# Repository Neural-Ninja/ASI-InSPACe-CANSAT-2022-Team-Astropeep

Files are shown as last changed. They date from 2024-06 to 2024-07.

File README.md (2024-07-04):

# ASI-InSPACe-CANSAT-2022-Team-Astropeep

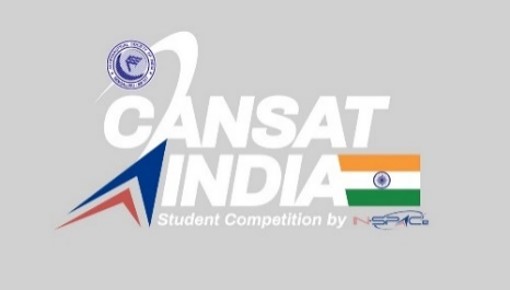
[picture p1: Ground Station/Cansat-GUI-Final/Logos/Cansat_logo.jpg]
CANSAT Design


This repository contains the project documentation and code for our team's (Team Astropeep) CanSat developed for the CanSat-India 2022 competition organized by Astronautical Society of India [(ASI)](https://www.asindia.org/), Indian National Space Promotion and Authorization Centre [(IN–SPACe)](https://www.inspace.gov.in) and Indian Space Research Organization [(ISRO)](https://www.isro.gov.in/). A CanSat is a miniature version of a real satellite, designed to fit within a small volume. Despite its miniature size, it mimics many of the functionalities and challenges of actual satellites. It is designed to perform specific scientific and engineering tasks, typically in a controlled flight environment such as a rocket launch or high-altitude balloon release. CanSats are used primarily in educational settings, particularly in STEM (Science, Technology, Engineering, and Mathematics) education programs, to teach students about satellite technology, space missions, data collection, and analysis.

## Introduction

This project details the development of our CanSat for the CanSat-India competition. Our goal was to design and build a functioning satellite within the constraints provided by the competition guidelines.

## Features

- Compact size (fits within a standard soda can)
- Integration of various sensors (e.g., temperature, pressure)
- Communication systems for data transmission
- Parachute deployment system
- Mechanical Gyro Control
- Data logging capabilities

## Components

The CanSat consists of the following main components:

- **Microcontroller**: Controls the operation and data collection.
- **Sensors**: Measure various environmental parameters (e.g., temperature, pressure).
- **Communication System**: Transmits data to the ground station.
- **Power System**: Provides necessary power to all components.
- **Mechanical Structure**: Holds all components securely and includes the parachute deployment system.
- **Mechanical Gyro Control**: Controls the orientation of CanSat during Descent.

## Technical Details

- **Microcontroller**: We used ESP-32 for processing and data handling.
- **Sensors**: Included BMP-280, DHT11 and MPU6050 to gather environmental data during flight.
- **Communication**: XBEE-Pro-S2C was employed for transmitting data to the ground station with 2.4 GHz of operating frequency.
- **Power**: Two Li-Ion battery (9V and 1200 mAh) was used to power the CanSat throughout its mission.

## Flight Software

The `Flight Software Files/` directory contains the source code used in the CanSat. It includes:

- **Main Control Code**: Handles sensor readings, data transmission, and overall control.
- **Sensor Calibration Scripts**: Scripts used for calibrating sensors pre-flight.
- **Data Logging Code**: Code snippets responsible for logging data during the flight.

## Ground Station

The `Ground Station/` directory contains the source code used in developing the ground station and GUI of CanSat. It includes:

- **GUI Scripts**: Handles sensor readings, data transmission, and overall control.
- **Communication Scripts**: Scripts used for calibrating sensors pre-flight.
- **Data Logging Code**: Code snippets responsible for logging data during the flight.

## 

## Usage

To replicate our CanSat project or use parts of our code, follow these steps:

1. Clone this repository:
    ```bash
       git clone https://github.com/Neural-Ninja/ASI-InSPACe-CANSAT-2022-Team-Astropeep.git
       cd ASI-InSPACe-CANSAT-2022-Team-Astropeep
2. Navigate to the `CANSAT Design Files/` directory for acessing the design CAD files.
     ```bash
        cd CANSAT Design Files
3. Navigate to the `CANSAT Presentation Files/` and `CANSAT Report Files/` for better conceptual understanding of our CANSAT model and its working. 
     ```bash
        cd CANSAT Presentation Files
        cd CANSAT Report Files
4. Navigate to the `Flight Software Files/` for accessing the Flight Software source codes.
    ```bash
        cd Flight Software Files
5. Navigate to the `Ground Station/` for accessing the Ground Station source codes
    ```bash
        cd Ground Station
## Contributing

Contributions to improve the code, documentation, or any other aspect of the project are welcome. Feel free to fork this repository, make your changes, and submit a pull request.

## License

This project is licensed under the [MIT License](License) - see the LICENSE file for details.

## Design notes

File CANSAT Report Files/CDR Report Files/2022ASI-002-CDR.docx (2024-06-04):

CANSAT 2022-23

Critical Design Review

(CDR)

TEAM ID: 2022ASI-002

TEAM NAME: ASTROPEEP

Serial N0. | CONTENTS
| Team description
| Sponsorship to CANSAT
| List of Acronyms
| System Overview
| Sensor Summary
| Mechanical Material Selection & Overview
| Mechanical Subsystem Analysis & Results
| Power Budget
| Mass Budget
| Actuator Design
| Control Mechanism of Gyroscope
| Trajectory & Descent Control
| Sensor Testing
| Communication & Data Handling
| Electrical Power Subsystem
| Flight Software Design
| GCS Deign & Over View
| CANSAT Algorithm
| Ground Station Final test Results
| CANSAT Ready to launch & Final test result
| CANSAT Integration & Testing
| Mission Operation and analysis
| Pre-flight requirement-check analysis
| Logistics and Transportation
| CANSAT ready to launch and final comments
| Conclusion

Team Description

FACULTY ADVISOR
Dr. Abhishek Rawat
MENTOR
Dr. Jagat Joyti Rath
MENTOR
Dhaval Joshi

Communication and Data handling
Risabh Raushan
Purvang Mistry
Akash Payghan
Ashotosh Jha
Software
Ashutosh Jha
Electronics
Akash Payghan
Victor Azad
Somesh Swami
Mechanical Analysis
Anuj Kumar Jha
Anuj Jha
TEAM LEADER
Victor Azad
Mechanical Design
Sagar Parihar
Victor Azad
Somesh Swami
Victor Azad
Ashutosh Jha

Sponsorship to CANSAT

We as Team Astropeep have received the sponsorship from different organisation and institutions, in form of money and in the form of goods.

List of sponsors are as mentioned below:

1. Institute of Infrastructure Technology Research and Management, Ahmedabad
2. Centre of Advanced Defence Technologies, IITRAM, Ahmedabad
3. Indian Studytech Services Pvt. Ltd., Dholpur, Rajasthan
4. Rudrabots Pvt. Ltd., Ahmedabad

List of Acronyms

Acronyms | Meaning
3D | 3-Dimensional
A | Analysis
cm | Centimeter
D | Demonstration
dB | Decibel
EPS | Electrical power Subsystem
FRR | Flight Readiness Review
FSW | Flight Software
GCS | Ground Control System
gm | Gram
GPS | Global Positioning System
GS | Ground Station
GUI | Graphical User Interface
Hz | Hertz
I | Inspection
I2C | Inter-Integrated Circuit
IC | Integrated Circuits
LED | Light Emitting Diode
PC | Personal Computer
QHA | Quasi Harmonic Function
RTC | Real Time Clock
T | Test
VM | Verification Method
GHz | Giga Hertz
s | Second
csv | Comma separated values
hrs | Hours
PCB | Printed Circuit Board
mAh | Milli ampere hour
m | Meter
V | Volts
FSS | Flight Software State

System Overview

MISSION SUMMARY

- Innovative Mechanical Gyro-control system that shall demonstrate the descent control of the CANSAT.
- CANSAT descent control system that shall open at an altitude of 500 m.

CANSATs will be launched to an altitude of 800.0 m to 900.0 m from the ground level and above the launch site & deployed near the peak altitude. During the ejection from the rocket orientation of the CANSAT is not controlled. The CANSAT must remain intact during the course of the entire mission and send the data to the ground station through a telemetry link.

Sr.no. | Requirement | Priority | Fulfillment | VM
| | | | A | I | T | D
1 | Total mass of the CANSAT shall be under 0.700 kg (+/- 0.050 kg) | High | Mass of Cansat is within limits. | x | | | X
2 | CANSAT shall fit in a cylindrical body of 0.125 m diameter x 0.310 m height. Tolerances are to be included to facilitate container deployment from the rocket fairing. | High | Cansat is designed with appropriate dimensions. | X | | | X
3 | Any sharp edges on the container body shall be avoided as it can cause interfere during the CANSAT ejection from the rocket. | High | No sharp Edges are present. | X | | | X
4 | Color of the CANSAT body shall be fluorescent i.e., pink, red or orange, and shall embody the Indian flag. | High | Color will be fluorescent and will embody Indian Flag. | | | | X
5 | The CANSAT shall consist of necessary sensors to provide the following mandatory Real-time datasets: Position data, altitude, pressure, temperature, orientation data, power data & system status. | High | Cansat has necessary sensors required for measuring mandatory data. | X | | | X
6 | Each data field shall be displayed in real-time on the ground station user interface/software. | High | GUI will be developed for displaying Data.
7 | CANSAT shall also record the data and save it into an onboard SD card in case of telemetry connection loss. | High | The data shall be recorded in SD Card.
8 | All electronics shall be enclosed and shielded from the environment. No electronics can be exposed except for sensors. There must be a structural enclosure. | High | No Electronics is exposed. | x | | | X
9 | CANSAT structure shall be built to survive 15 Gs of launch acceleration & 30 Gs of shock. | High | CANSAT will survive required shock. | | | | X
10 | The CANSAT shall have an external power switch with an indicator light or sound for being turned on or off, in order to avoid the de-assembling of CANSATs on the launch pad. | High | CANSAT has an external power switch. | x | | | X
11 | The CANSAT shall contain a total of 2 descent control mechanisms, to be used at different stages while descent. | High | has 2-descent control mechanism. | | | | x
12 | CANSAT shall immediately deploy the first parachute after ejection from the rocket. | High | 1st parachute will be immediately deployed after ejection. | | | | X

# Sensor Systems Summary and Test results

Selected Component | Type | Function | Interface
Adafruit BMP 280 | Pressure and temperature sensor | Measures air pressure and temperature both in the payload and the container | I2C
Matek SAM M8Q | GPS | Gets payload coordinates (latitude and longitude), GPS time, and GPS satellite | Serial
Voltage divider | Voltage Sensor | Measures voltage of the payload’s battery | ADC
MPU6050 | Acceleration and Orientation Sensor | Orientation and Acceleration Measurement | ADC

Sensor | Model | Function
Altimeter Sensor | BMP280 | Altitude Measurement
Air Pressure and Air Temperature Sensor | BMP280 | Pressure and Temperature Measurement
Acceleration and Orientation Sensor | MPU6050 | Orientation and Acceleration Measurement
GPS Receiver Sensor | Matek SAM M8Q | Latitude, Longitude, Altitude, Time, Satellites number Measurement
Voltage Sensor | Voltage Divider , CPU’s ADC Converter | Power Status

# Payload Air Pressure Sensor

# Summary (1 of 2)

Sensor-Adafruit BMP 280

Pressure Range (hPa) | Operating Voltage (V) | Weight (g) / Dimension (mm) | Current Consumption (uA) | Resolution (Pa) | Accuracy (hPa) | Interface | Data Format
300-1250 | 1.65 – 3.6 | 1.2 21.6 x 16.6 | 2.7 | 0.016 | ±0.08 | I2C, SPI | Float XXXXX.XX (Pa)

Altitude above sea level can be calculated from Barometric Equation below. However, output from sensor is very noisy so that a kalman filter will be used to estimate the pressure value.

Barometric Equation

# Descent Control Design

Sample Output

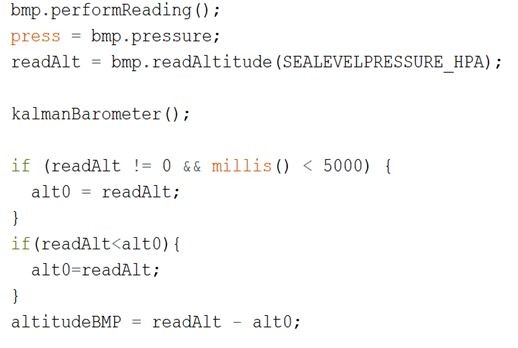
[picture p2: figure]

Kalman Filter

Data Processing

Sensor | | | | Adafruit BMP 280
Temperature Range (°C) | Operating Voltage (V) | Weight (g) / Dimension (mm) | Current Consumption (uA) | | Resolution (Pa) | Accuracy (hPa) | Interface | Data Format
0 – 65 | 1.65 – 3.6 | 1.2 21.6 x 16.6 | 2,7 | | 0.016 | ±0.08 | I2C, SPI | Float XX.XX (C)

# Payload Air Pressure Sensor Summary

# (2 of 2)

# Temperature data will be collected and processed with the help of Adafruit_BMP3XX library. No further processing is needed as the reading is very stable.

Sample Output

Data Processing

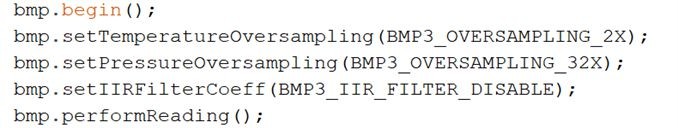
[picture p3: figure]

# GPS Sensor Summary

Sensor | Matek SAM M8Q + Compass

Tracking Sensitivity (dBm) | Operating Voltage (V) | Weight (g) / Size (mm) | Current Consumption (mA) | Channel | Accuracy (m) | Interface | Update Rate (Hz) | Data Format
-165 | 4-6 | 7 20 x 20 x 10 | 29 | 72 | ~2.5 | UART | 18 | Float and Integer

Longitude, latitude, and the other data will be collected and processed with the help of Tiny GPS Plus library by Mikal Hart. This sensor can lock onto GPS satellite quickly.

Data Processing

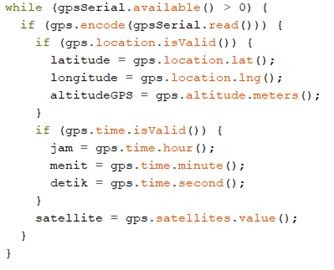
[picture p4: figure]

Sample Output

# Left to right:

# Hour, minute, second, latitude, longitude, altitude, satellite

Source: https://github.com/mikalhart/TinyGPSPlus/blob/master/src/TinyGPS%2B%2B.h

# Payload Voltage Sensor Summary

Name | Range (V) | Error rate (%) | Interface | Data Format
Processor Analog Pin (Voltage Divider) | 0 - 5 | 0.03 | ADC | Float X.XX (Volt)

# Battery voltage is measured using the ADC port trough a voltage divider, the following resistors are used in the circuit.

R1 = 1 MΩ

R2 = 100 kΩ

The ATSAMD Processor ADC has maximum resolution of 32-bit with 3.3 volt analog reference, but the resolution used is 16-bit resolution. So, the maximum accuracy of this on board voltage sensor is 50 uV..

Sample Output

Data Processing

# Gyroscope Sensor Selection Summary :

Sensor | Range (°/s) | Resolution (bit) | Accuracy (°/s) | Data Interface | Operating Voltage (V) | Cost (Rs.) | Dimension (mm) | Weight (gm)
MPU6050 | ±250 | 16 | 1.9 | I2C/IIC | 3-5 | 120 | 4 X 4 X 0.9 | 3

# Reason for selecting MPU6050 :

# Light weight, small size and Low Cost.

# Using same sensor for acceleration and orientation measurement will reduce the cost and weight of Cansat.

Team Id:2022ASI-002 AstroPeep

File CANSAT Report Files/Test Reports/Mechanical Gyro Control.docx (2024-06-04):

# Control Mechanism of Gyroscope

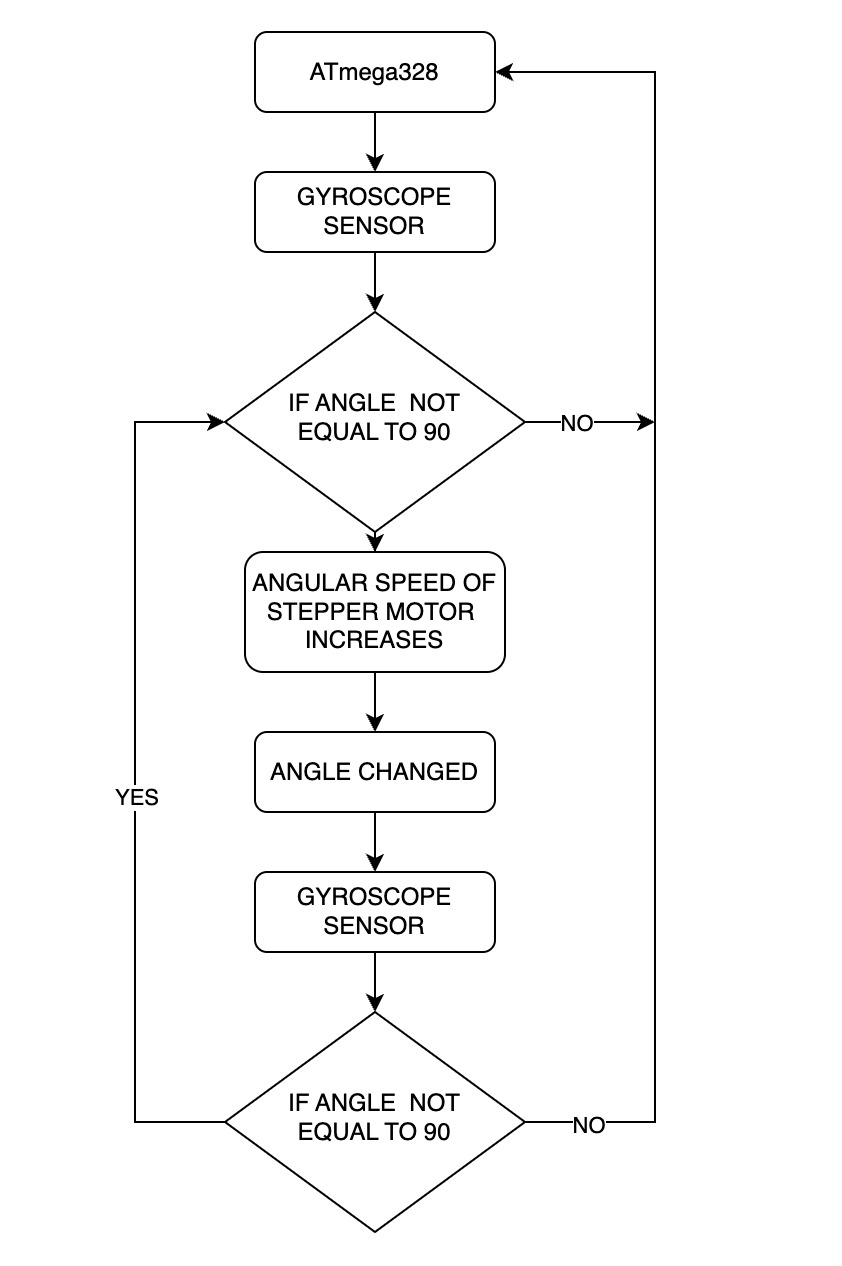
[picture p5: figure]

With the help of ATMEGA-328, gyroscope sensor detect the orientation of our CANSAT. If the angle detected by gyroscopic sensor is not equal to 90 ° i.e., our CANSAT is not perfectly straight then the angular speed of stepper motor attached to our gyroscope increases and thus our gyroscope applied force on the CANSAT to make it perpendicular. The angular speed increases uptill the CANSAT is not aligned perpendicularly.

Once our CANSAT is aligned perpendicularly the angular speed of stepper motor remains constant. Whenever an external force is applied to our CANSAT, accordingly the speed of stepper motor increases or decreases in order to align our CANSAT 90 ° .

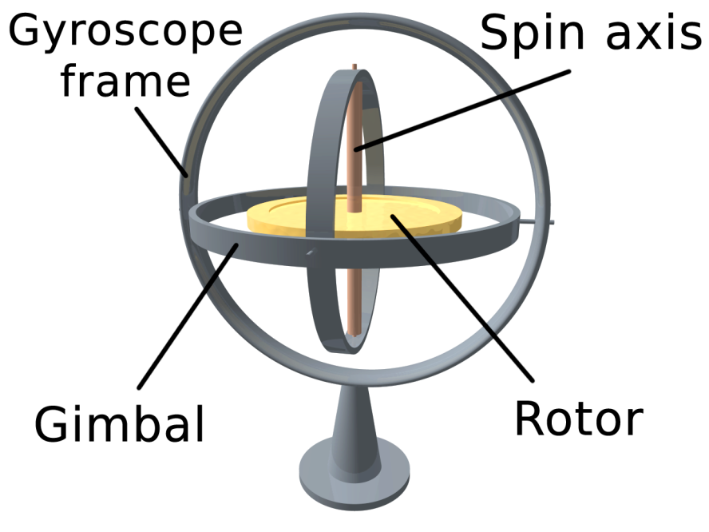
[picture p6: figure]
Gyroscope - Wikipedia

CANSAT India Students Competition by ASI: Team Id:2022ASI-002 AstroPeep

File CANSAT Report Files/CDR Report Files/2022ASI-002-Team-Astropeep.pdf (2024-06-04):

# CANSAT 2022-23

Team Id:2022ASI-002
AstroPeep

# Critical Design Review (CDR)

# TEAM ID: 2022ASI-002

# TEAM NAME: ASTROPEEP

Team Id:2022ASI-002

AstroPeep

## Serial N0. CONTENTS

## 1. Team description

## 2. Sponsorship to CANSAT

## 3. List of Acronyms 4. System Overview

## 5. Sensor Summary 6. Mechanical Material

| Selection & Overview

## 7. Mechanical Subsystem

| Analysis & Results

## 8. Power Budget 9. Mass Budget

## 10. Actuator Design

## 11. Control Mechanism of

| Gyroscope

## 12. Trajectory & Descent Control

## 13. Sensor Testing

## 14. Communication & Data

| Handling

## 15. Electrical Power Subsystem

## 16. Flight Software Design

## 17. GCS Deign & Over View

## 18. CANSAT Algorithm

Team Id:2022ASI-002

AstroPeep

## 19. Ground Station Final test Results 20. CANSAT Ready to launch & Final test result

## 21. CANSAT Integration & Testing

## 22. Mission Operation and analysis

## 23. Pre-flight requirement-check analysis 24. Logistics and Transportation 25. CANSAT ready to launch and final comments 26. Conclusion

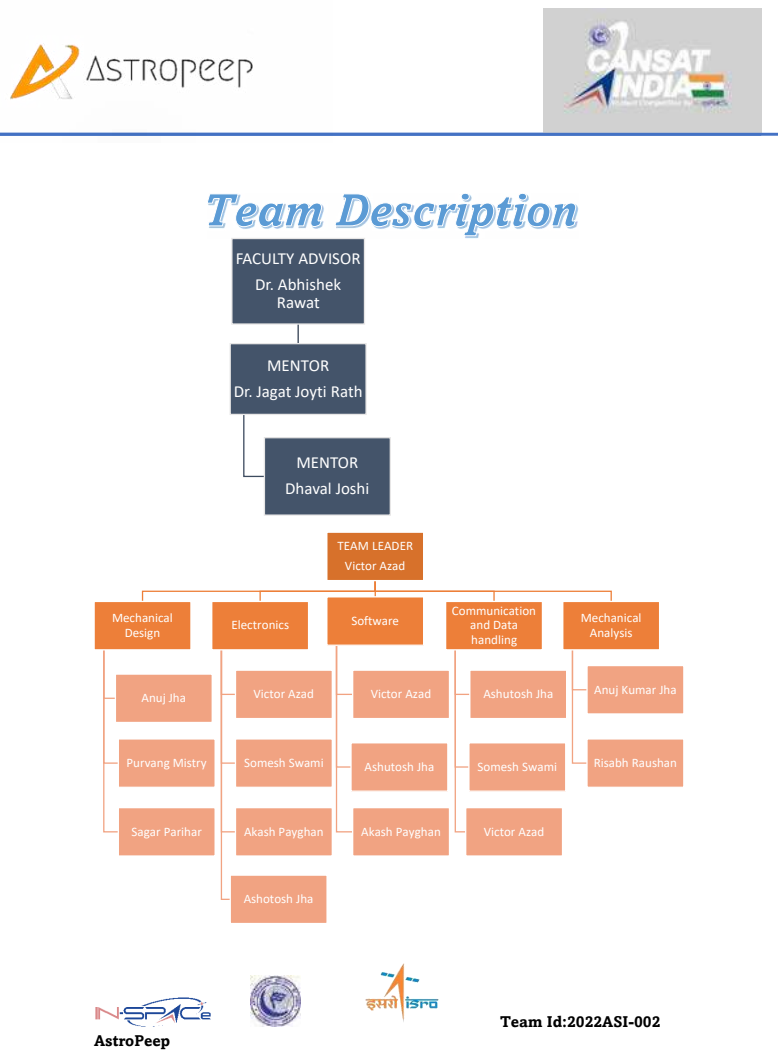
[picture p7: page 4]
Team Id:2022ASI-002; AstroPeep; FACULTY ADVISOR; Dr. Abhishek Rawat; MENTOR; Dhaval Joshi; TEAM LEADER; Victor Azad; Mechanical Design; Anuj Jha; Purvang Mistry; Sagar Parihar; Electronics; Somesh Swami; Akash Payghan; Ashotosh Jha; Software; Ashutosh Jha; Communication and Data handling; Mechanical Analysis; Risabh Raushan

MENTOR
Dr. Jagat Joyti Rath

Anuj Kumar Jha

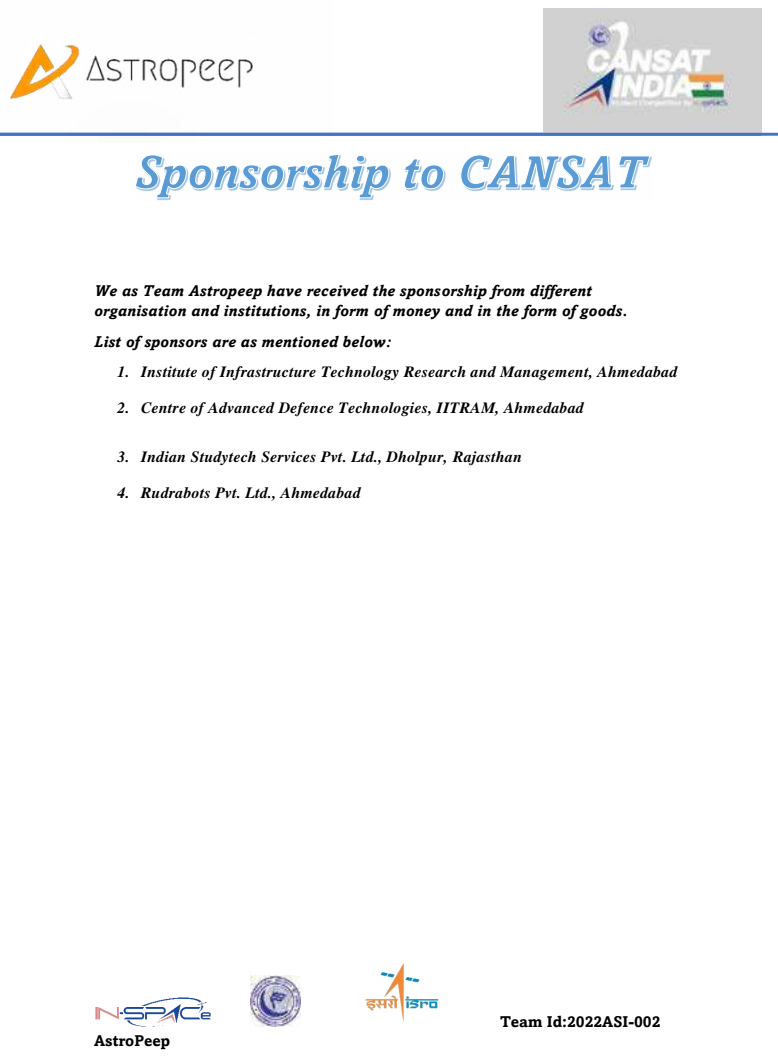
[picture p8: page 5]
Team Id:2022ASI-002; AstroPeep

We as Team Astropeep have received the sponsorship from different
organisation and institutions, in form of money and in the form of goods.

List of sponsors are as mentioned below:

1. Institute of Infrastructure Technology Research and Management, Ahmedabad

2. Centre of Advanced Defence Technologies, IITRAM, Ahmedabad

3. Indian Studytech Services Pvt. Ltd., Dholpur, Rajasthan

4. Rudrabots Pvt. Ltd., Ahmedabad

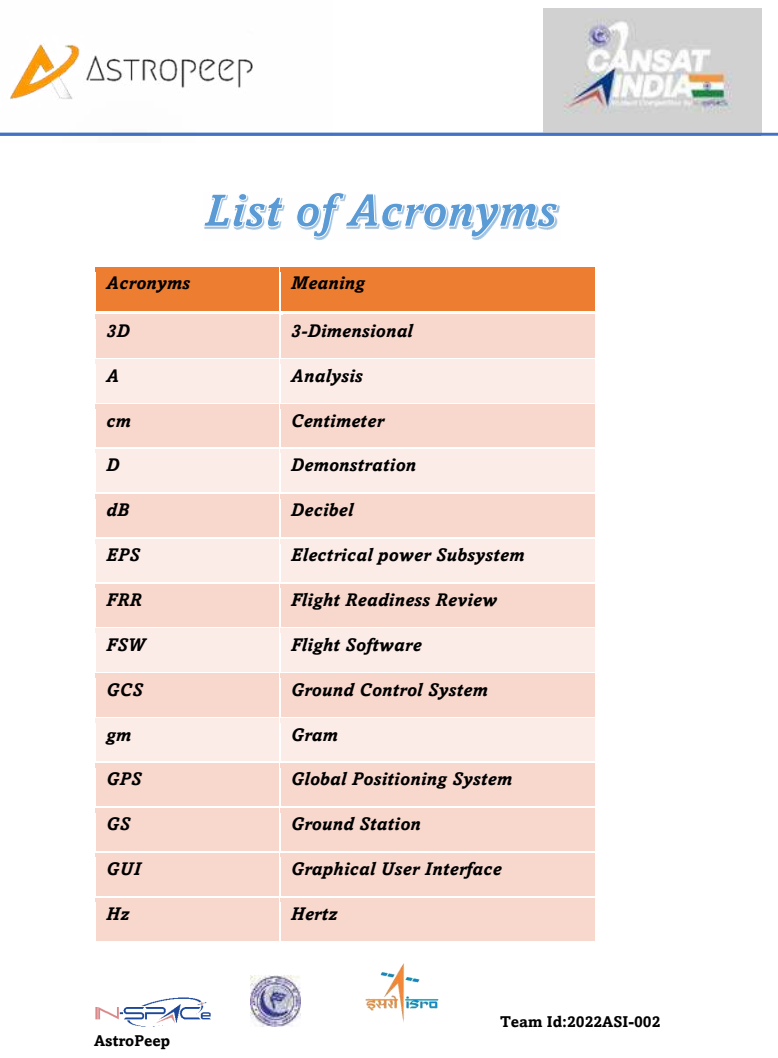
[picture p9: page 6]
Team Id:2022ASI-002; AstroPeep; Acronyms; Meaning; 3-Dimensional

A Analysis

cm | Centimeter

D Demonstration

dB | Decibel

EPS | Electrical power Subsystem

FRR | Flight Readiness Review

FSW | Flight Software

GCS | Ground Control System

gm | Gram

GPS | Global Positioning System

GS | Ground Station

GUI | Graphical User Interface

Hz | Hertz

Team Id:2022ASI-002

AstroPeep

I Inspection

I2C | Inter-Integrated Circuit
IC | Integrated Circuits
LED | Light Emitting Diode
PC | Personal Computer
QHA | Quasi Harmonic Function
RTC | Real Time Clock

T Test

VM | Verification Method
GHz | Giga Hertz
s | Second
csv | Comma separated values
hrs | Hours
PCB | Printed Circuit Board
mAh | Milli ampere hour
m | Meter

V Volts

FSS | Flight Software State

Team Id:2022ASI

-002

AstroPeep

Team Id:2022ASI-002

AstroPeep

MISSION SUMMARY

- Innovative Mechanical Gyro-control system that shall demonstrate the

descent control of the CANSAT.

- CANSAT descent control system that shall open at an altitude of 500

m.

CANSATs will be launched to an altitude of 800.0 m to 900.0 m from the ground

level and above the launch site & deployed near the peak altitude. During the

ejection from the rocket orientation of the CANSAT is not controlled. The

CANSAT must remain intact during the course of the entire mission and send the

data to the ground station through a telemetry link.

Sr.no. | Requirement | Priorit y | Fulfillment | VM
A | I | T | D
1 Total mass of the CANSAT shall be | under 0.700 kg (+/- 0.050 kg) | High | Mass of Cansat is within limits. | x | X
2 CANSAT shall fit in a cylindrical | body of 0.125 m diameter x 0.310 m height. Tolerances are to be included to facilitate container deployment from the rocket fairing. | High | Cansat is designed with appropriate dimensions. | X X
3 Any sharp edges on the container | body shall be avoided as it can cause interfere during the CANSAT ejection from the rocket. | High | No sharp Edges are present. | X X

Team Id:2022ASI-002

AstroPeep

4 Color of the CANSAT body shall be | fluorescent i.e., pink, red or orange, and shall embody the Indian flag. | High | Color will be fluorescent and will embody Indian Flag. | | X
5 The CANSAT shall consist of | necessary sensors to provide the following mandatory Real-time datasets: Position data, altitude, pressure, temperature, orientation data, power data & system status. | High | Cansat has necessary sensors required for measuring mandatory data. | X X
6 Each data field shall be displayed | in real-time on the ground station user interface/software. | High | GUI will be developed for displaying Data.
7 CANSAT shall also record the data | and save it into an onboard SD card in case of telemetry connection loss. | High | The data shall be recorded in SD Card.
8 All electronics shall be enclosed and | shielded from the environment. No electronics can be exposed except for sensors. There must be a structural enclosure. | High | No Electronics is exposed. | x | X
9 CANSAT structure shall be built to | survive 15 Gs of launch acceleration & 30 Gs of shock. | High | CANSAT will survive required shock. | | X
10 The CANSAT shall have an external | power switch with an indicator light or sound for being turned on or off, in order to avoid the de-assembling of CANSATs on the launch pad. | High | CANSAT has an external power switch. | x | X
11 The CANSAT shall contain a total | of 2 descent control mechanisms, to be used at different stages while descent. | High | has 2-descent control mechanism. | | x

Team Id:2022ASI-002

AstroPeep

### 12 CANSAT shall immediately deploy

the first parachute after ejection from the rocket.

High 1st parachute will be immediately deployed after ejection.

X

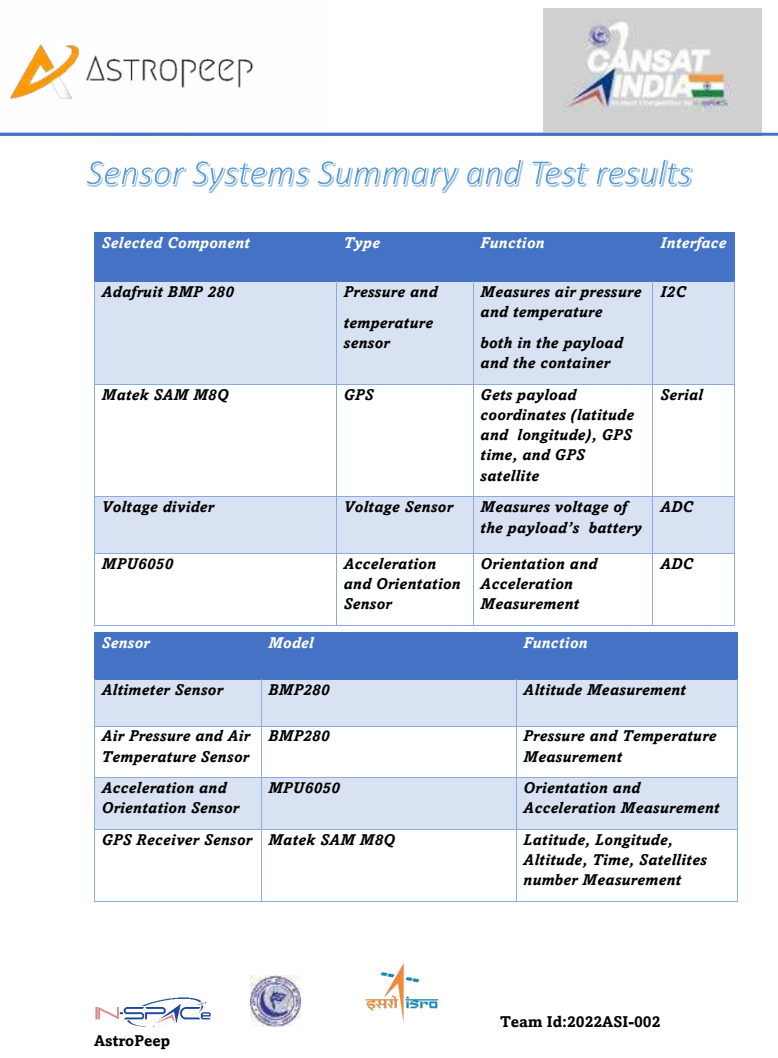
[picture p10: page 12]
Team Id:2022ASI-002; AstroPeep; Selected Component; Type; Function; Interface; Sensor; Model

Adafruit BMP 280 | Pressure and temperature sensor | Measures air pressure and temperature both in the payload and the container | I2C

Matek SAM M8Q | GPS | Gets payload coordinates (latitude and longitude), GPS time, and GPS satellite | Serial

Voltage divider | Voltage Sensor | Measures voltage of the payload’s battery | ADC

MPU6050 | Acceleration and Orientation Sensor | Orientation and Acceleration Measurement | ADC

Altimeter Sensor | BMP280 | Altitude Measurement

Air Pressure and Air Temperature Sensor | BMP280 | Pressure and Temperature Measurement

Acceleration and Orientation Sensor | MPU6050 | Orientation and Acceleration Measurement

GPS Receiver Sensor | Matek SAM M8Q | Latitude, Longitude, Altitude, Time, Satellites number Measurement

Team Id:2022ASI-002

AstroPeep

Voltage Sensor | Voltage Divider , CPU’s ADC Converter

Power Status

Team Id:2022ASI-002

AstroPeep

# Payload Air Pressure Sensor Summary (1 of 2)

## Sensor-Adafruit BMP 280

Pressure
Range
(hPa)

Operating
Voltage
(V)

Weight (g)
/
Dimension
(mm)

Current
Consumption
(uA)

Resolution
(Pa)

Accuracy
(hPa)

Interface Data
Format

300-
1250

1.65 – 3.6 1.2

### 21.6 x

16.6

2.7 | 0.016 | ±0.08 | I2C, SPI | Float XXXXX.XX (Pa)

Altitude above sea level can be calculated from Barometric Equation below. However, output from sensor is very noisy so that a kalman filter will be used to estimate the pressure value.

## Barometric Equation

## Sample Output

### Data Processing

Team Id:2022ASI-002
AstroPeep

### Kalman Filter

Team Id:2022ASI-002

AstroPeep

# Payload Air Pressure Sensor Summary

(2 of 2)

## Temperature data will be collected and processed with the help of

## Adafruit_BMP3XX library. No further processing is needed as the

reading is very stable.

# GPS Sensor Summary

Sensor | Adafruit BMP 280
Temperature Range (°C) | Operating Voltage (V) | Weight (g) / Dimension (mm) | Current Consumption (uA) | Resolution (Pa) | Accuracy (hPa) | Interface | Data Format
0 – 65 | 1.65 – 3.6 | 1.2 21.6 x 16.6 | 2,7 | 0.016 | ±0.08 | I2C, SPI | Float XX.XX (C)
Data Processing | Sample Output

Tracking Sensitivity (dBm); Operating Voltage (V); Weight (g) / Size (mm); Current Consumption (mA); Channel Accuracy (m); Interface Update Rate (Hz); Data Format; UART; Float; and Integer

Team Id:2022ASI-002

AstroPeep

Sensor | Matek SAM M8Q + Compass

Longitude, latitude, and the other data will be collected and processed with the help of Tiny GPS Plus library by Mikal Hart. This sensor can lock onto GPS satellite quickly.

## Data Processing

Team Id:2022ASI-002

AstroPeep

# Left to right:

Hour, minute, second, latitude, longitude,

# altitude, satellite

# Payload Voltage Sensor Summary

Name | Range (V) | Error rate (%) | Interface | Data Format
Processor Analog Pin (Voltage Divider) | 0 - 5 | 0.03 | ADC | Float
| | | | X.XX (Volt)

## Battery voltage is measured using the ADC port trough a voltage

divider, the following resistors are used in the circuit.

## R1 = 1 MΩ

## Sample Output

### Source: https://github.com/mikalhart/TinyGP SPlus/blob/master/src/TinyGPS%2B %2B.h (https://github.com/mikalhart/TinyGPSPlus/blob/master/src/TinyGPS%2B%2B.h)

Team Id:2022ASI-002

AstroPeep

## R2 = 100 kΩ

The ATSAMD Processor ADC has maximum resolution of 32-bit with 3.3 volt analog reference, but the resolution used is 16-bit resolution. So, the maximum accuracy of this on board voltage sensor is 50 uV..

## Data Processing

## Sample Output

Team Id:2022ASI-002

AstroPeep

# Gyroscope Sensor Selection Summary :

Sensor | Range (°/s) | Resolution (bit) | Accuracy (°/s) | Data Interface | Operating Voltage (V) | Cost (Rs.) | Dimension (mm) | Weight (gm)
MPU6050 | ±250 | 16 | 1.9 | I2C/IIC | 3-5 | 120 | 4 X 4 X 0.9 | 3

## Reason for selecting MPU6050 :

➢Light weight,small size and Low Cost.

## ➢Using same sensor for acceleration and orientation measurement will reduce the cost and weight of

Cansat.

CANSAT India Students Competition by ASI:

Team Id:2022ASI-002 AstroPeep

# Innovative Materials Selection:

## Material Proposed as in PDR:

As in Preliminary Design Report (PDR) of our CANSAT had:

Serial No. | Component | Previous Material | Modified material
1. | Outer Body Panels | ABS Polycarbonate Sheets | ABS Polycarbonate Sheets
2. | Vertical Rods | 2024 T3 Al Alloy | CFRP Z-100
3. | Horizontal Bases | 2024 T3 Al Alloy | CFRP Z-100
4. | Circular Support Rings | -- | CFRP Z-100
5. | Top Lid | Polyethene Film | Polyethene Film
6. | Parachute & Chords | Ripstop Nylon | Ripstop Nylon

Reason to Change Materials:

- The change in the material of the structure including the Vertical Rods, Horizontal bases and the circular ring support were previously proposed as to be made up of 2024 T3 Al Alloy which is replaced by Carbon Fiber Reinforced Plastic (CFRP) because of the following reasons:

### 1. Stress-Strain Curve:

Lower yield point of the Aluminium in general which would have led to the increase in the deformation as compared to that of the CFRP. Also the ductility as a property in not needed for our use.

### 2. Availability:

Market availability of the Aluminium and it’s alloy is very rare due to the import and export restrictions and also due to the scarcity in the global market and so is not the case with the CFRP Z-100 as the spools, sheets, rods, and plates all are available in the local market.

### 3. Economics:

The cost of Aluminum is too high and cannot fit in the budget constrain of CANSAT whereas cost of CFRP is relatively lower than 2024 T3 Al Alloy.

# Material Acquisition:

- Material for prototype testing was received in early January 2023 but it was sample piece used to validate our own mathematical model as computed.
- Material to be used in the fabrication of the main structure have been ordered and are in process.
- We have received all our electronical components as ordered for the testing and analysis purposes.

Changes | in | Mechanical | Design

# Dimensions

Changes Made | Previous Dimensions | Previous | New Dimensions | New
Increased Rod Diameter in Battery and Gyro Compartment | 5 mm | | 7 mm
Increased thickness of Base Plate and Parachute 2 Base Plate | 2 mm | | 5 mm
Increased Parachute 1 Base Plate thickness | 2 mm | | 7 mm
Added a support Plate to increase strength in Parachute 2 Container | 0 mm | | 5 mm
Added a hook to grab parachute | - -

# Physical layout:

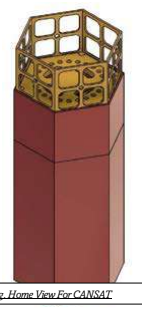
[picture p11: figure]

Fig. Home View For CANSAT | Fig. Home View of CANSAT without body panels
Fig. Top View of CANSAT | Fig. Bottom View of CANSAT

# Damping

To deal with the vibration and shock due to thrust of launching vehicle. We have planned of adding up foam and carbon fiber shock dampers to the PCB plates, servo housing, battery setup, camera module and buzzer module.

All the components are a vital part of the CANSAT and for the proper data acquisition all of the components has to be damped against vibration.

Types of Damping Used:

- Shock Absorber for the PCB and Battery plates:
- Shock Absorbing Foam Padding being used for servo motors used for ejection mechanism and gyroscope control:

- Rubber Shock Absorber are being used for the screws which are being used to

mount the Outer Body Panel on the CANSAT Frame:

# System Configuration Concepts:

## Selected Design Concept of PDR:

As proposed in the Preliminary Design Review (PDR) round held in the September 2022. We have the following design concept proposed:

Fig. Concept 1 Design Proposed

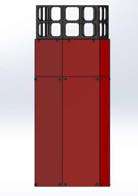
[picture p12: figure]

Fig. Concept 1 Design Dimensions

## Design Analysis:

All the below mentioned results were analyzed to simulate the

- Total Deformation:

This is to check deformation along the yaw, pitch & roll caused due to the axial loadings.

- Equivalent stress:

According to the Von-mises Theory, the Equivalent Stress or Von-mises Stress, is most used criteria for checking yield conditions for any structure.

- Stress Intensity:

This is to check the magnitude of the stress generated in a particular component in the CANSAT.

- Shear Stress:

It is the stress generated at the edge of the structure of CANSAT parallel to the vertical axis i.e. the roll axis of the CANSAT.

## CANSAT PDR Proposed Design:-

This is the structure considered for the design analysis of the CANSAT which includes the vertical solid rods and hexagonal plates which all are in a single piece as they are 3-D printed using the Carbon Fibre Spool with a re-inforced packing.

Fig. Structure considered for the analysis.

The meshing for the structure is considered of 0.0008 m (meters) with a Path Conforming Tetrahedron mesh elements. The mesh wash fully programme controlled.

The forces are assumed to act in the center of top and bottom plates as the there is a hook in the center of the Top Plate for tying the Parachute Chords to it. Also, we have considered the force due to acceleration of gravity at the center of the CANSAT.

For the same meshed structure, the solution goes as follows:

1. Total Deformation:

Fig. Total Deformation/Distortion in the CANSAT

2. Equivalent Stress:

Fig. Window Showing Equivalent Stress in

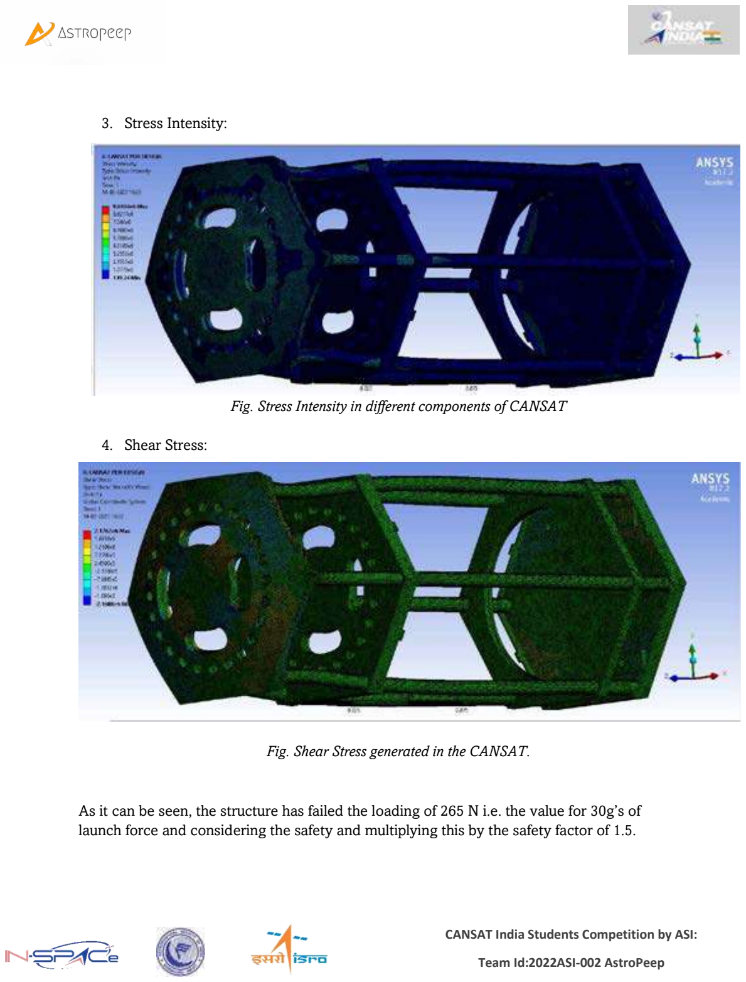
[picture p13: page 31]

3. Stress Intensity:

Fig. Stress Intensity in different components of CANSAT

4. Shear Stress:

Fig. Shear Stress generated in the CANSAT.

As it can be seen, the structure has failed the loading of 265 N i.e. the value for 30g’s of launch force and considering the safety and multiplying this by the safety factor of 1.5.

Observation:

Looking to the simulation results achieved and as discussed about the change in the material, we have found out that the structure fails if constructed out of normal Carbon Fiber spool with this amount of loading.

Conclusion:

To avoid any such failure during the launch or ascent we then decided to go with the Carbon Fiber Reinforced Polymer. And adding up a extra horizontal support to the structure and replacing the hollow hexagonal faced pipes with the solid circular faced rods.

Solution Derived:

For the same three different design versions were prepared and analyzed. The changes to the CANSAT were as follows:

1. Increasing the Diameter of the Vertical Rods
2. Adding Up a circular ring to the compartment deforming
3. Increased Diameter of rods with a circular ring added to the deforming compartment.

Out of all these the 3rd design alteration gave us the best possible results which is as follows:

## CANSAT Improved Design & Analysis:

The design proposed after the alteration is as follows:

The solution to the analysis with the same constraint as of the previous one is as follows:

1. Total Deformation: (Negligible Distortion was observed)

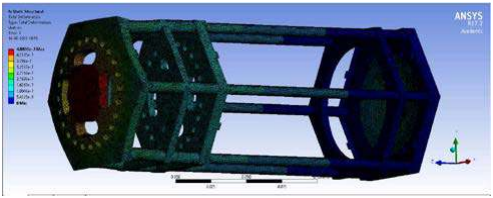
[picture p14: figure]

Fig. No/ Negligible Deformation Observed

2. Equivalent Stress:

Fig. Reduction In the Equivalent(Von-Mises) Stress of the CANSAT

3. Stress Intensity:

Fig. Reduction in the Stress Intensity generated in the components.

4. Shear Stress:

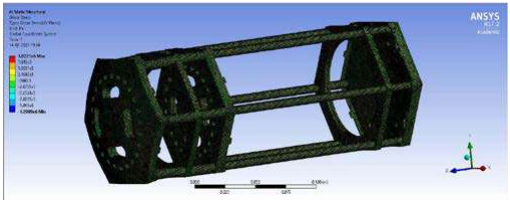
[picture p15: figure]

Fig. Decrement in the Shear Stresses around the CANSAT

Conclusion:

Looking to the results observed we hereby consider this particular design of structure of CANSAT to be the best fitted for our purpose.

# Power Budget:

We use a double cell Lithium-Ion battery to power the main system. The battery has a nominal voltage of 9v and maximum capacity of 600mAh each. Allows up to 2 hours of duration of operation. The Battery is lightweight and compact. Well known battery manufacturer.

Component | Power Consumption (Wh)
CPU (ATmega328) | 0.238
Pressure Sensor (BMP 280) | 0.007392
Acceleration and Gyro Sensor (MPU6050) | 0.02574
GPS Module | 0.792
XBEE | 0.726
Servo Motor (Mechanical Gyro Control) | 3.32
Servo Motor (Parachute Ejection)(x2) | 12.24
Buzzer | 0.792

In the above Budget Power Consumption is calculated for a period of 2 hrs on assumption that CanSat may be turned on for 2h, while the actual flight time might be less than that.

Total Power Drained from the Battery for 2 hrs operation = 5.369772 Wh.

## Changes Made After PDR:

Battery configuration used to power our CANSAT has been changed from Series to ‘Parallel’. This enables us for proper stepping down of voltage according to the requirements using the voltage divider system.

# Mass budget:

## Method of correction:

In case any error occurs the lower part will be equipped with extra space for increasing weight with screws and nuts. Initially it will include 6 screws that can be detached if the structure is too heavy.

Margin = 500 – 497.1 = 2.9g

Part | Mass Contributed (in g)
PC ABS Panels | 43.79 ± 0.2
Aluminium Rods | 61.33 ± 0.2
Base Plate | 22 ± 0.2
Parachute 1 CF Container | 54.84 ± 0.2
Parachutes | 90 ± 0.2
Shackle | 10 ± 0.2
Carbon Fiber tube | 30.28 ± 0.2
Dampers and Foam | 30 ± 0.5
Screws, Washers and nuts | 20.25 ± 0.2
Servos | 27 ± 0.2
Other 3-D printed parts | 20 ± 0.2
PCB 1 | 75 ± 0.5
Camera | 20 ± 0.2
PCB 2 | 40 ± 0.5
Gyroscope | 22 ± 0.2
Wiring | 25 ± 0.5
Batteries | 105 ± 0.2

TOTAL MASS = 696.49 ± 4.6 g = 701.09 g

ALLOWED LIMIT = 700 ± 50 g = 750 g

## Changes Made After PDR:

Minor revisions were made in the mass calculations.

# Actuator Design:

As proposed in the previous design concept of PDR we were having a setup of Pogo Pins to release the Parachute 2 after achieving a height of 500m. But due to guidelines and mission requirements prohibiting the usage of spring in the CANSAT, we decided to find a substitute parachute deployment system.

After further consideration we are using the following configuration, pair of servo motors

and actuators system.

Fig. Placement and Alignment of Servo Motors Acting as the driving element of Actuator Design of Ejection Mechanism

Fig2. Servo-actuator is holding the parachute 1 base plate until reaching 500m.

Block diagram for working of actuator system for parachute deployment,

GPS sensor with the help of ATmega328 detect the position of our CANSAT from ground. When the height of our CANSAT goes below 450m, it triggers our servo motors and thus unlocked the upper chamber of our CANSAT, releasing the secondary parachute.

# Control Mechanism of Gyroscope

## With the help of ATMEGA-328, gyroscope sensor detect the orientation of our CANSAT. If the angle detected by gyroscopic

## sensor is not equal to 90° i.e., our CANSAT is not perfectly straight then the angular speed of stepper motor attached to our gyroscope increases and thus our gyroscope applied force on the CANSAT to make it perpendicular. The angular speed increases uptill the

CANSAT is not aligned perpendicularly.

## Once our CANSAT is aligned perpendicularly the angular speed of stepper motor remains constant. Whenever an external force is applied to our CANSAT, accordingly the speed of stepper motor

increases or decreases in order to align our CANSAT 90°.

# Summary of Trajectory control:

## 1. The average wind speed of DHOLERA is thy month of June is 20km/hr. that’s why we consider the horizontal

velocity of our CANSAT is to be 20km/hr.

## 2. In the first line of decent i.e. from 850 m to 500 m the vertical velocity of CANSAT is 20km/hr. Thus during this period of time our CANSAT travels the horizontal

distance of 350 m.

3. In the second line of our decent i.e. from 500m to ground our CANSAT travels the speed of 4km/hr. thus the horizontal distance travel by our CANSAT is 2500 m 4. Thus when combining the horizontal distance travelled in the first as well as second line of decent is 2500m plus 350m is equal to 2850m i.e. 2.85 km 5. Thus we know how far our CANSAT can reach from our ground station, thus we know that we have to design antenna with the range of 3-4 km, so that we can communicate with our CANSAT when it reach to

ground.

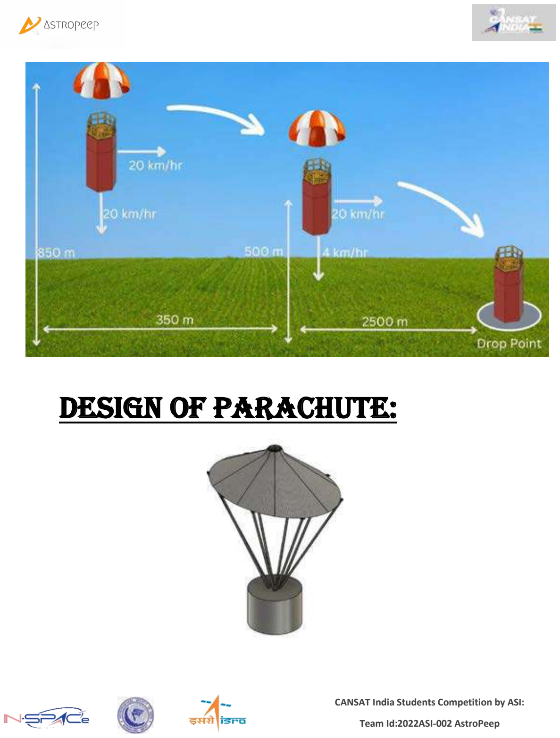
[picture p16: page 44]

# Design of Parachute:

# SENSORS TESTING PROCEDURE & SUMMARY

- Each of the sensors was tested on the breadboard with the use of the required software and the microcontroller. The accuracy of the data obtained from each sensor was checked.
- Then the sensor tests were carried out in a combined manner.

# CDH

- The communication between the microcontroller and the sensors was tested.
- The communication between the receiver and transmitter XBee were tested using the XCTU Software for the competition distance requirements (600-800 meters).
- The gain test of the antenna was tested using the XCTU Software.
- The data transmission altitude requirement (750 meters) in competition will be tested via drone. Then, the data transmission speed and the accuracy of the data sent to the ground station will be checked.

# EPS

Prototype circuit was installed on the perforated plate and breadboard. It was checked if it works with the required power supply.
The total current of the system was measured. Calculated and measured values were compared. The melt of fishline circuit was installed and the break time of the melt was measured.
The MOSFET used in circuit was triggered with 3.3V to check its operation.
It will be checked whether there is a short circuit on the PCB.

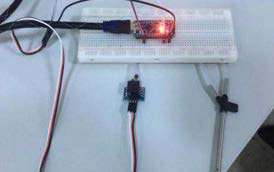
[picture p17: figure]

Caption

# Radio Communication

- The XBees setting was done over XCTU software. NETID/PANID and baud rate accuracy was checked.
- The XBee communicates in unicast mode. XBees do not broadcast, the XBees only communicate with each other.
- Data received from the sensors on the circuit will be transmitted to the ground station via XBee. The data will be checked from the ground station interface.
- The sufficiency of the computer battery was tested for 2 hours.
- We continue the tests as we have started at the PDR stage.

# MECHANICAL

- Delta wing folding mechanism was tested (hinge, rotating joint, stretched fabric elastic and telescopic system).
- The sufficiency of the delta wings for descenting was tested at different altitudes.
- The CanSat's mechanical tests will be checked (separation, drop and fit check etc.).
- The payload release mechanism will be tested with FSW.
- The CanSat's subsystems durability before and after the test flights will be checked.
- The CanSat will be checked for the given environmental test requirements.
- Thanks to the folding mechanism designers in our team. It fits well into the container.
- The camera stabilization will be achieved by actively controlling payload with rudder and elevator using servo motors

# Decent Control

- The installed electronic circuit will be placed in the payload and it will be tested at 450 meters via the drone.
- The payload’s delta wings will be tested for gliding in a circular pattern with a radius of 250 meters from 450 meters to above 100 meters (actively controlled for one minute). Its aerodynamic suitability will also be checked during the test.
- Active control of the payload will be provided with rudder and elevator using the servo motors. The opening of the payload’s parachute will be tested at an altitude above 100 meters.

# FSW

- The accuracy of the data get from the each sensors were checked (particulate/dust, air speed, GPS location, temperature, pressure, etc.).
- Sub-systems were tested (release mechanisms, parachute opening, communication, etc.).
- Data recovery algorithms were tested in case of microcontroller reset.
- The sequence of the data transmission to the ground station will be checked for consistency in the appropriate order.

Sample of Data received

# Communication and Data Handling Subsystem Design

## Below is the communication Subsystem overview :

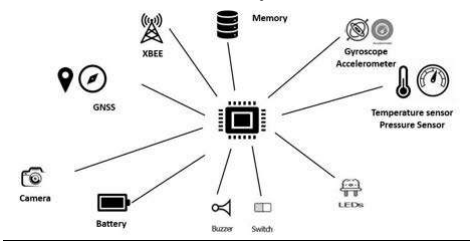
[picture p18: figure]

Fig. Communication and Data Handling Overview

Changes made after PDR in communication subsystem and data handling :

PDR | CDR | Rationale

Main processor
was STM32F103

Main processor is changed to ATMega-328.

Due to problems faced in programming STM32F103 and because of previous experience of team in working with ATMega-328 and also meets all the requirements.

# Telemetry

- Upon powering up, the CANSAT collects the required telemetry at a 1 Hz sample rate.
- The telemetry data is being transmitted with ASCII comma separated fields followed by a carriage return in the following format :
- <TEAMID>,<TIMESTAMPING>,<PACKETCOUNT>,<ALTITUDe>,<PRESSURE >,<TEMP>,<VOLTAGE>,<GPSTIME>,<GPS LATITUDE>,<GPS LONGITUDE>, <GPS ALTITUDE>,<GPS SATS>,<ACCELEROMETER DATA>, <GYRO SPIN RATE>, <FLIGHT SOFTWARE STATE>,<ANY OPTIONAL DATA>
- The received telemetry for the entire mission will be saved on the ground station computer as a comma-separated value (.csv) file with name of file as 2022-ASI-002.csv

The NET ID/PAN ID of the Xbee is set to team no. as per the requirements and its setting is shown below :

Fig. . Xbee 1 Setting for NET/PAN ID

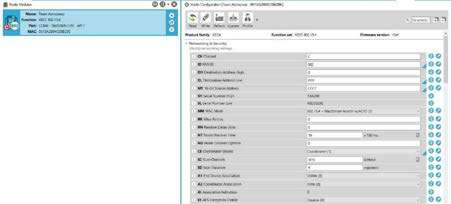
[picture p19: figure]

Fig. Xbee 2 Setting for NET/PAN ID

# TELEMETRY DATA FORMAT

TM Parameter | Function | Resolution /Format
<TEAM ID> | Team Number | 2022ASI-002
<TIME STAMPING> | Time since the initial power | Seconds
<PACKET COUNT> | Count of transmitted packets | Integer
<ALTITUDE> | Altitude in units of meters and must be relative to ground | 0.1 meters
<PRESSURE> | Measurement of atmospheric pressure | 1 pascal
<TEMP> | Temperature in Celsius | 0.01℃
<VOLTAGE> | Voltage of the CANSAT power bus | 0.01 Volts
<GPS TIME> | Time generated by the GPS receiver | Seconds
<GPS LATITUDE> | Latitude generated by the GPS receiver | 0.0001 degrees
<GPS LONGITUDE> | Longitude generated by the GPS receiver | 0.0001 degrees
<GPS ALTITUDE> | Altitude generated by the GPS receiver | 0.1 meters

# Communication and Link Budget

Some changes are done in which we revisited the Gain calculation of receiving and transmitting antenna and we rectified accordingly as shown below.

Fig. Communication and Link Budget

# Calculation :

- Transmitted Power : 8 dB
- Transmitter Antenna Gain : 5.94 dB
- Transmitter Loss : 1 dB
- Free Space Loss : 110.14 dB
- Miscellaneous Loss : 1 dB
- Receiver Antenna Gain : 11.1 dB
- Receiver Loss : 1 dB
- Received Power : -84.14 dB
- Receiver Sensitivity : -101 dB
- Link Margin : 16.86 dB

# Antenna Selection

There is no changes since PDR just we simulated the radiation pattern of antennas and found the gains accordingly.

## GCS Antenna

Antenna Design :

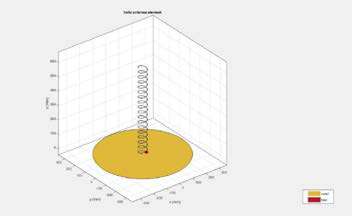
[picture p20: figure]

Antenna Radiation Pattern :

Antenna Design Code :

## CANSAT Antenna

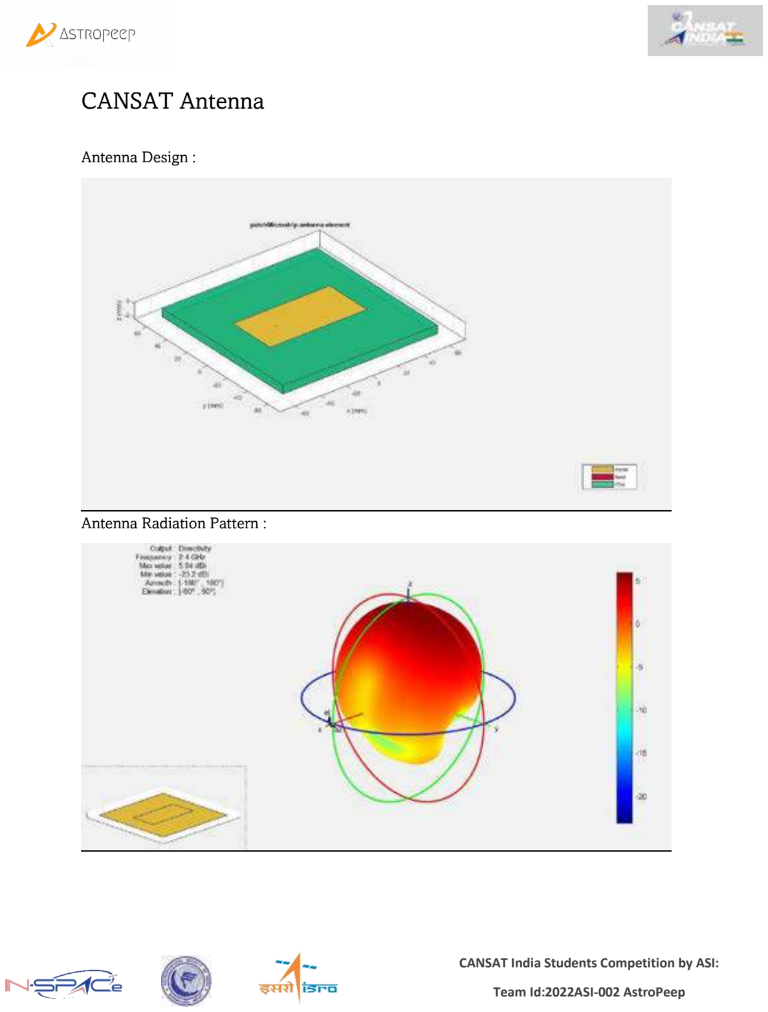
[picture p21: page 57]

Antenna Design :

Antenna Radiation Pattern :

Antenna Design Code :

The gain obtained after analysis are :

- GCS Antenna – 11.1 db
- Cansat Antenna – 5.94 db

An after calculating we rectified the changes in the Communication and Link Budget.

# Electrical POWER SUBSYSTEM

## There are only some minor changes in Electrical power subsystem as mentioned below :

- The battery configuration is changed from series to parallel which made the step down process more efficient.
- The position of switch is also modified from bottom to panel side of CANSAT.

# Electrical Block Diagram

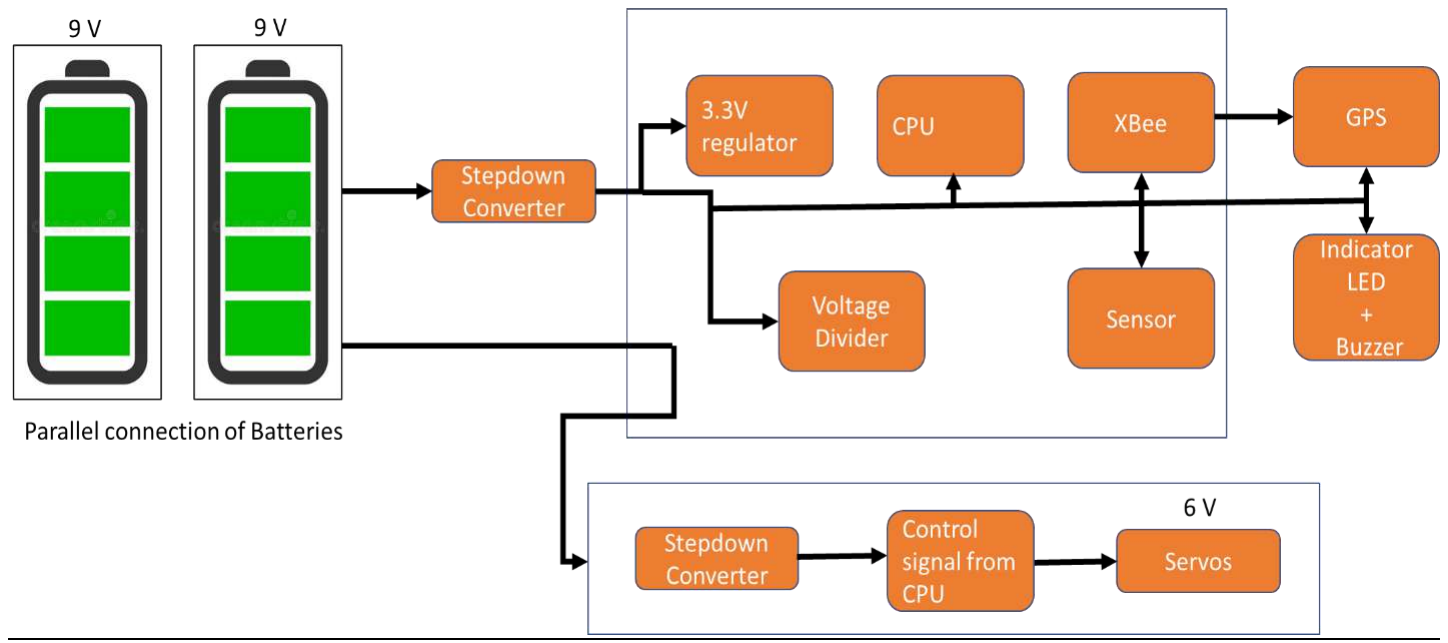
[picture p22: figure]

Fig. Electrical Power Subsystem Block Diagram

# Flight Software design

## Overview of the CanSat FSW Design

- The CanSat will collect sensor data then save to SD card and send to ground station via XBee.
- The CanSat will deploy 2nd Parachute deploy mechanism after reaching 500m altitude.
- The buzzer will keep beeping after landing until turned off with power switch.

## Programming Language

- C/C++ for CanSat container
- Python/C++ for ground station

## Development Environment

- Arduino IDE
- Visual Studio Code
- Spyder

Fig. Flight Software Design Overview

## Momentary Power Cut Precaution Strategy :

As far as power management goes, all devices are ON for all time except two (Servo motor for Deployment of 2nd Parachute and Buzzer for recovery) as Servo motor will deployed only for some time after crossing critical altitude (500m) and Buzzer will be turned ON after landing for location and recovery of CanSat.

After reset of processor in flight mode, previous state of mission together with last packet count can be retrieved from flash.

This information with current GNSS time is sufficient to continue mission.

# GCS Design and Overview

## Overview

- Main Computer is a laptop running GS application. The application is configured in GUI so that an appropriate port and baud rate can be selected.
- QHA antenna receives data from the probe (i.e. CanSat CPU) and transmits commands.
- Xbee PRO S2C module forwards and receive data to form communication link between CanSat and GCS.
- GS application, written in C++/Python, saves and displays data. It also saves received data in a local area network.

There is no changes since PDR.

## Data Flow and Components

- The antenna receives data over radio from the probe.
- Using Xbee explorer cable , forwards data to the Xbee module.
- Xbee PRO S2C module forwards data to GS’s Main Computer using micro USB to USB cable.
- Software developed in C++ parses and then displays data in engineering units and save them into a CSV file.
- Main computer is capable of sending predefined commands to the probe.

## Progress Since PDR :

- The login page of GUI is completed and currently working on dashboard page of GUI and the overall data receiving software is tested for sensors individually.
- The development of helical antenna of GCS is started.

## Ground Control Station GUI :

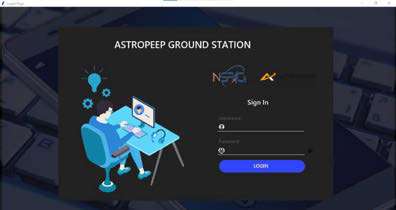
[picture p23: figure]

Fig. GCS GUI login page

The GUI is build using SPYDER IDE using Python language and the work is still in progress the login page is build as shown above and the dashboard work is in progress and for testing we individually tested the sensor by sending data using our microprocessor and plotted graph in the SPYDER IDE using Python function matplotlib.

The screenshots of code written in SPYDER IDE are attached below :

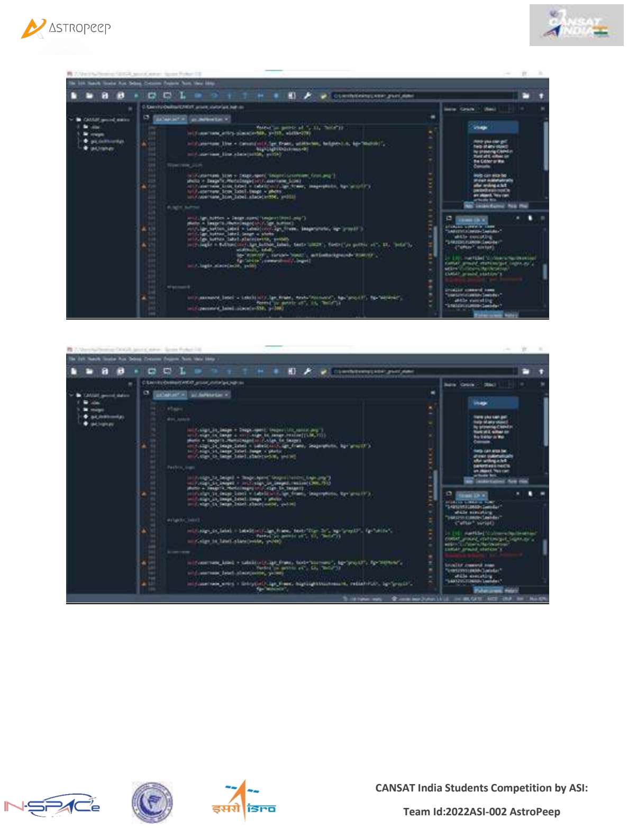
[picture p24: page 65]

The development of dashboard were all the data will be plotted is in progress and after development the dashboard will be like as shown below :

Fig. GCS GUI Dashboard

# CANSAT algorithm

The CANSAT algorithm is developed in C/C++ language using Visual Studio Code and Arduino IDE and the flow chart of the algorithm is shown below :

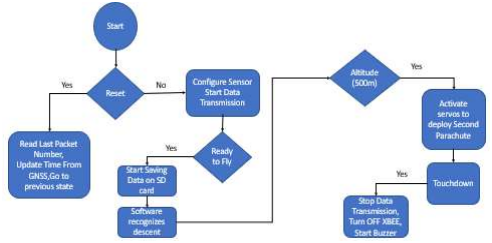
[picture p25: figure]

Fig. CANSAT Algorithm Flow Chart

# Ground Station final test results

The Cansat Ground Station final test results is still in progress as the test of data collection is done individually for all the sensors and in next step we will be combining the overall data into our GUI.

Our GUI work is also still in progress and final glimpse of our GUI is shown below:

The test result plots of the individual sensor data are shown below:

Fig. CANSAT GUI Dashboard

Altitude Test Plot:

Pressure Test Plot:


Temperature Test Plot :


The testing of some of the components are still in progress like GPS , Gyroscope and Accelerometer.We are still working on the testing of the above mentioned components.

# CANSAT Integration and Testing

## Testing before Integration :


The above mentioned steps are for testing the cansat before integration and after this testing we will go ahead for integration.

## Integration of CANSAT :

- As our primary structure fabrication process which will let be a homogenous structure with no mechanical joints.
- Other than this the outer body panels will be connected using the shock absorbing screws.
- Batteries , PCB and Servo motors are connected to the particular damper used which are then connected to the structure of CANSAT using screws and other mechanical joints as shown below.

Fig. CANSAT Integration Stage 1


Fig. CANSAT Integration Stage 2

# Mission Operation and Analysis

# Pre-flight requirement-check-analysis

## Setting up GS

• Computer and Antenna; Communication Test; Pre-Flight check and Tests; • Structure • Electronics • DCS components

## Cansat Integration

- Container assembly

## CanSat recovery

# Logistics and transportation:

For the Logistics and Transportation:

- We will be packing the fragile and non-secured elements independently using cartons and bubble wraps.
- Whereas other all the elements will be packed in a wooden sheet box by using Thermocol sheets, Bubble Wraps, Cardboard and Straps as per the requirements of the fabricated model of CANSAT.

# CANSAT ready to launch

and final comments.

- The testing was made on similar kind of prototypes and we found the rectifications in the model as observed.
- Accordingly, we have made changes and as of that our software part is almost done however in Hardware our work is still in progress.
- Due to the delay in the delivery of the materials and the electronic components required for the final fabrication of the CANSAT.
- The work will be completed in accordance to the availability of material however all the analysis, simulations and test results are completed through the alternative scale models of the similar materials.

# Conclusion

## Accomplishments

- Telemetry is tested.
- GCS GUI is developed up to some extent.
- Antenna testing is completed.
- Mechanical analysis (Stress-strain , Vibration and Fit check) is completed.

## Unfinished work

- The fully integrated electronic & mechanical subsystem are not entirely functional yet and needs to be tested.
- Prototypes are being tested and more refinements are required.
- Flight software is in progress.

## Next stage of development

- Final Fabrication work completion
- Code Review
- Testing of integrated system
- Assembly of complete CANSAT
- Integrated testing of CANSAT.

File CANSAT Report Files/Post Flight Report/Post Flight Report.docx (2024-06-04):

# CanSat Final Report

# Acknowledgement

The journey of CanSat has been long and tedious but no doubt it was very interesting and we as participants are very delighted and happy with the opportunity provided to us through CanSat Competion organized by INSPACE. We appreciate INSPACE, ISRO & ASI for organising this event and giving us such platform to work with our friends despite being of different educational streams which showed the importance of collaboration with others of different background complimenting our lack of knowledge in those departments and helping us excel in big and complex projects involving various expertise. The most dreading thing during any competition is the attitude of the jury members and their responses to our team’s progress, we are proud to say and glad that we had some of the best jury members who evaluated our efforts accordingly and supported us in improving our Project through their guidance and gentle sweet advices which we found very motivating.

We would also like to express our gratitude towards our college for supporting us and guiding us throughout the process. Despite several obstacles faced and failures encountered we are glad that the institute still kept faith in us.

We would further like to extend our thanks to our sponsor Rudrabots for believing in us all the way to the end.

A team can not perform to its fullest unless it has got a good guidance and hence we would like to thank our mentor Dr. Abhishek Rawat for believing and guiding us through this exciting CanSat Journey.


# CanSat after Recovery

# CanSat Launch and Recovery Distance


# Data Collected on micro SD Card

# Conclusion

Team Id:2022ASI-002

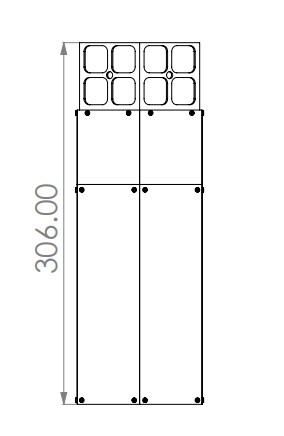
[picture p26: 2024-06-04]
Drawing Files/design.jpeg

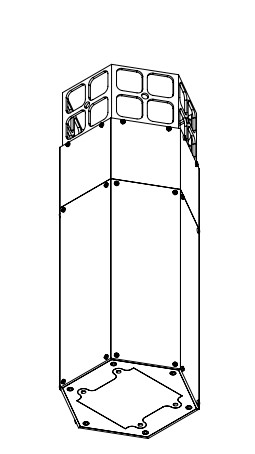
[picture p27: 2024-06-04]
Drawing Files/design 2.jpeg

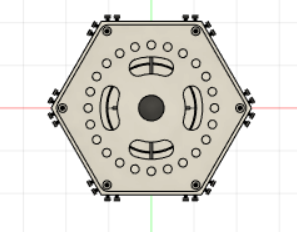
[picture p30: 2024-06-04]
Drawing Files/Isometric Structural Top View.png

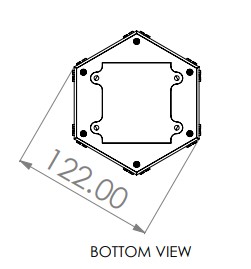
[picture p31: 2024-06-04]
Drawing Files/Bottom view.jpeg

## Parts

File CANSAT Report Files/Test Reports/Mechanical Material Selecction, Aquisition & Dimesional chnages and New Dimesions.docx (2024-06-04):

## Innovative Materials Selection:

### Material Proposed as in PDR:

As in Preliminary Design Report (PDR) of our CANSAT had:

Serial No. | Component | Previous Material | Modified material
1. | Outer Body Panels | ABS Polycarbonate Sheets | ABS Polycarbonate Sheets
2. | Vertical Rods | 2024 T3 Al Alloy | CFRP Z-100
3. | Horizontal Bases | 2024 T3 Al Alloy | CFRP Z-100
4. | Circular Support Rings | -- | CFRP Z-100
5. | Top Lid | Polyethene Film | Polyethene Film
6. | Parachute & Chords | Ripstop Nylon | Ripstop Nylon

Reason to Change Materials:

- The change in the material of the structure including the Vertical Rods, Horizontal bases and the circular ring support were previously proposed as to be made up of 2024 T3 Al Alloy which is replaced by Carbon Fiber Reinforced Plastic (CFRP) because of the following reasons:
1. Stress-Strain Curve:

Lower yield point of the Aluminium in general which would have led to the increase in the deformation as compared to that of the CFRP. Also the ductility as a property in not needed for our use.

2. Availability:

Market availability of the Aluminium and it’s alloy is very rare due to the import and export restrictions and also due to the scarcity in the global market and so is not the case with the CFRP Z-100 as the spools, sheets, rods, and plates all are available in the local market.

3. Economics:

The cost of Aluminum is too high and cannot fit in the budget constrain of CANSAT whereas cost of CFRP is relatively lower than 2024 T3 Al Alloy.

## Material Acquisition:

- Material for prototype testing was received in early January 2023 but it was sample piece used to validate our own mathematical model as computed.
- Material to be used in the fabrication of the main structure have been ordered and are in process.
- We have received all our electronical components as ordered for the testing and analysis purposes.

## Changes in Mechanical Design Dimensions

Changes Made | Previous Dimensions | Previous | New Dimensions | New

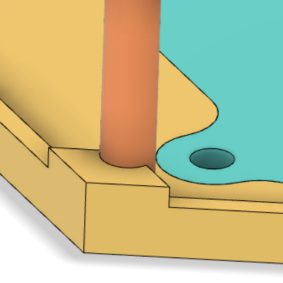
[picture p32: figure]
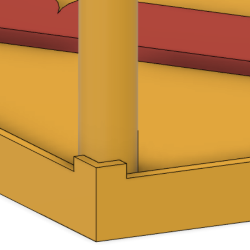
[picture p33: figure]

Increased Rod Diameter in Battery and Gyro Compartment | 5 mm | | 7 mm

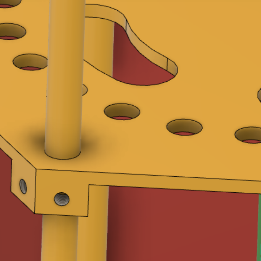
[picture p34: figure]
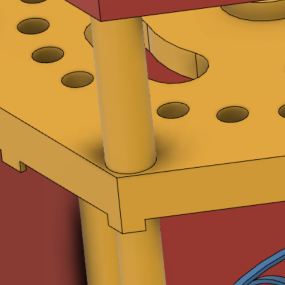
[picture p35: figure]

Increased thickness of Base Plate and Parachute 2 Base Plate | 2 mm | | 5 mm

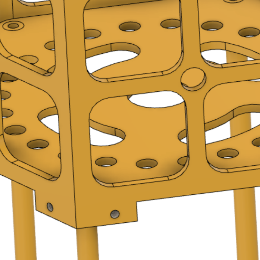
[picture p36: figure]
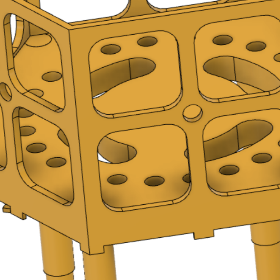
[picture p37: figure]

Increased Parachute 1 Base Plate thickness | 2 mm | | 7 mm

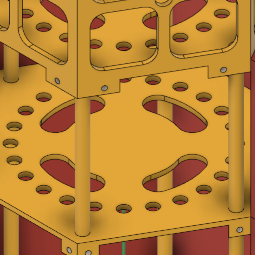
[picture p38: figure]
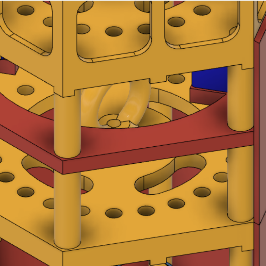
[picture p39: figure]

Added a support Plate to increase strength in Parachute 2 Container | 0 mm | | 5 mm


Added a hook to grab parachute | - | | -


# Physical layout:

# Fig. Home View of CANSAT without body panels

# Fig. Home View For CANSAT


# Fig. Bottom View of CANSAT

# Fig. Top View of CANSAT

CANSAT India Students Competition by ASI: Team Id:2022ASI-002 AstroPeep

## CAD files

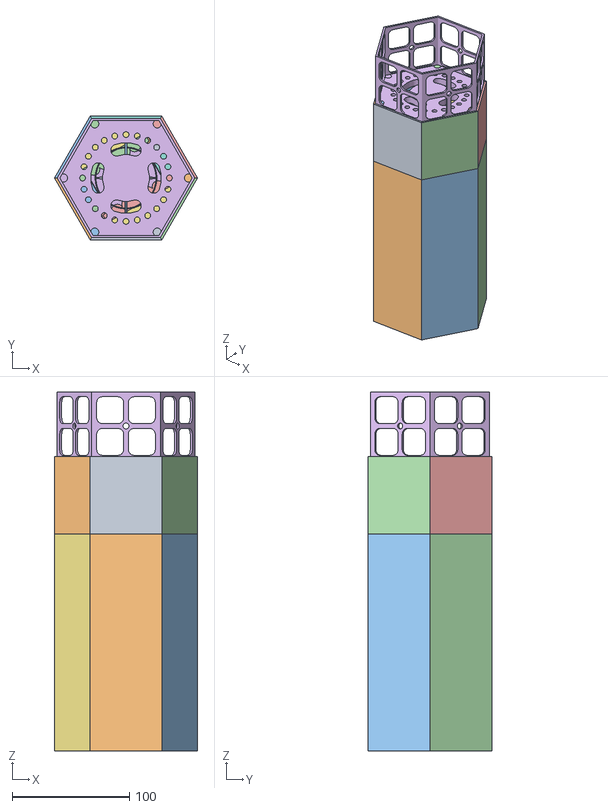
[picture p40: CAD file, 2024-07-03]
Ground Station/Cansat-GUI-Final/CANSAT@2 v7 v16.obj
122.0 x 105.7 x 306.0

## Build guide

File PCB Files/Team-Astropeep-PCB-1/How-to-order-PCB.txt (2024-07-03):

How to Order PCB

Please refer to:
https://docs.easyeda.com/en/PCB/Order-PCB

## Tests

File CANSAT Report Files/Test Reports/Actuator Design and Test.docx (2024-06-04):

## Actuator Design:

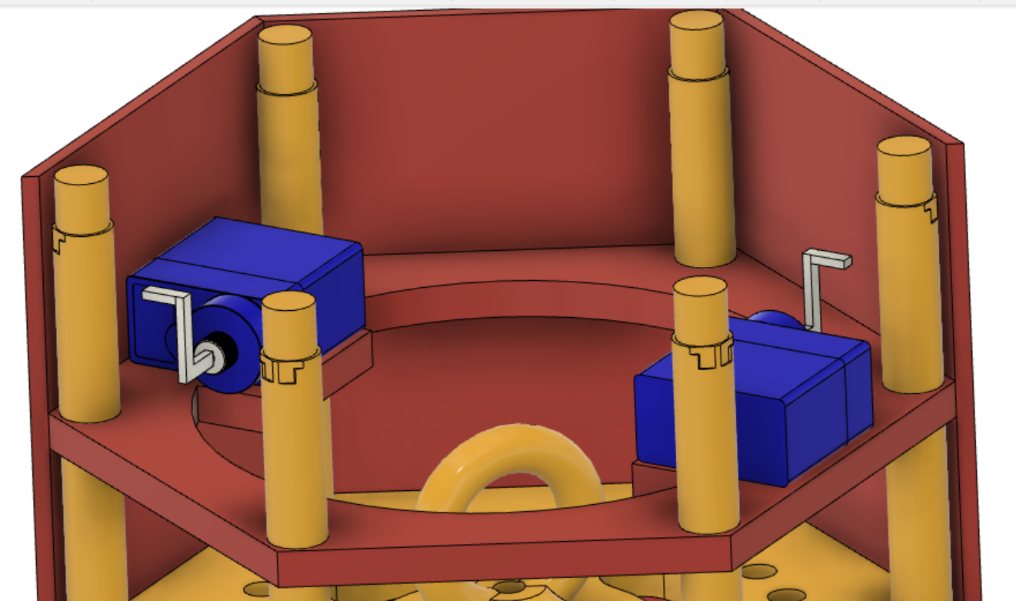
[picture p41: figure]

As proposed in the previous design concept of PDR we were having a setup of Pogo Pins to release the Parachute 2 after achieving a height of 500m. But due to guidelines and mission requirements prohibiting the usage of spring in the CANSAT, we decided to find a substitute parachute deployment system.

After further consideration we are using the following configuration, pair of servo motors and actuators system.

# Fig. Placement and Alignment of Servo Motors Acting as the driving element of Actuator Design of Ejection Mechanism

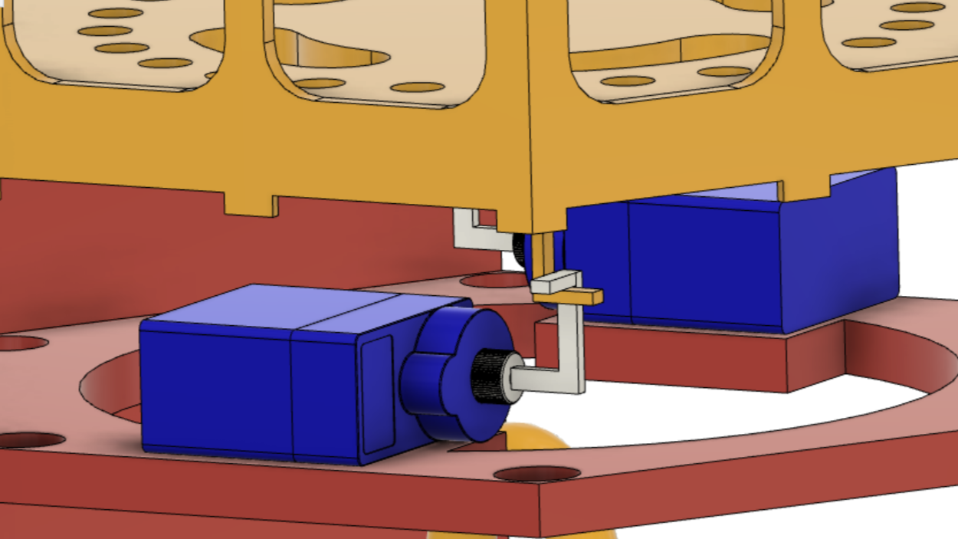
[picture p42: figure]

Fig2. Servo-actuator is holding the parachute 1 base plate until reaching 500m.

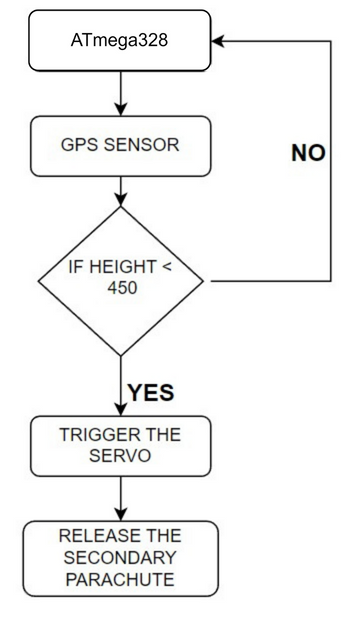
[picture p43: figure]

Block diagram for working of actuator system for parachute deployment,

GPS sensor with the help of ATmega328 detect the position of our CANSAT from ground. When the height of our CANSAT goes below 450m, it triggers our servo motors and thus unlocked the upper chamber of our CANSAT, releasing the secondary parachute.

CANSAT India Students Competition by ASI: Team Id:2022ASI-002 AstroPeep

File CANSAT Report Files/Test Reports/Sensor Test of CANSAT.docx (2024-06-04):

# SENSORS

- Each of the sensors was tested on the breadboard with the use of the required software and the microcontroller. The accuracy of the data obtained from each sensor was checked.
- Then the sensor tests were carried out in a combined manner.

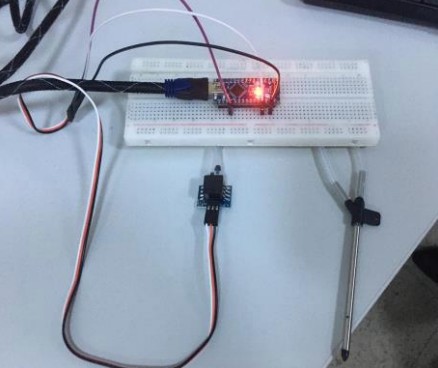
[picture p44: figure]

# CDH

- The communication between the microcontroller and the sensors was tested.
- The communication between the receiver and transmitter XBee were tested using the XCTU Software for the competition distance requirements (600-800 meters).
- The gain test of the antenna was tested using the XCTU Software.
- The data transmission altitude requirement (750 meters) in competition will be tested via drone. Then, the data transmission speed and the accuracy of the data sent to the ground station will be checked.

# EPS

Prototype circuit was installed on the perforated plate and breadboard. It was checked if it works with the required power supply.

The total current of the system was measured. Calculated and measured values were compared. The melt of fishline circuit was installed and the break time of the melt was measured.

The MOSFET used in circuit was triggered with 3.3V to check its operation. It will be checked whether there is a short circuit on the PCB.

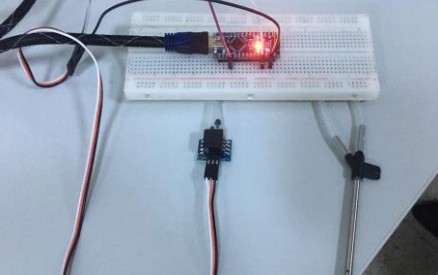
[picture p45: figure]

Caption

# Radio Communication

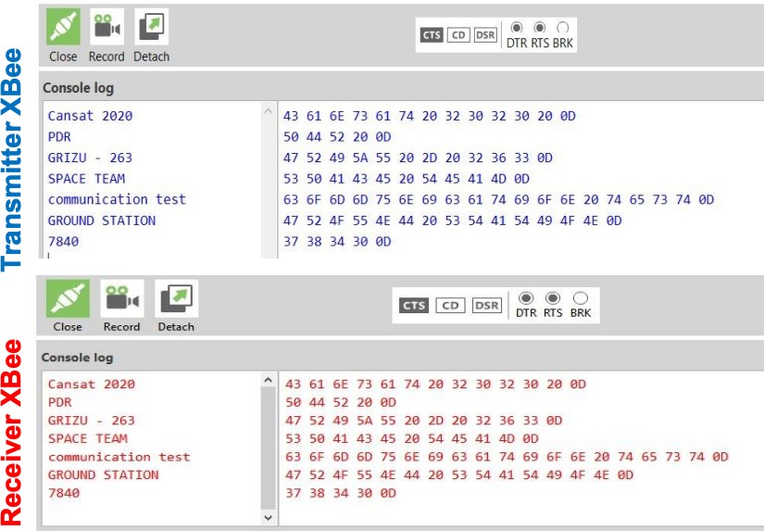
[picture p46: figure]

- The XBees setting was done over XCTU software. NETID/PANID and baud rate accuracy was checked.
- The XBee communicates in unicast mode. XBees do not broadcast, the XBees only communicate with each other.
- Data received from the sensors on the circuit will be transmitted to the ground station via XBee. The data will be checked from the ground station interface.
- The sufficiency of the computer battery was tested for 2 hours.
- We continue the tests as we have started at the PDR stage.

# MECHANICAL

- Delta wing folding mechanism was tested (hinge, rotating joint, stretched fabric elastic and telescopic system).
- The sufficiency of the delta wings for descenting was tested at different altitudes.
- The CanSat's mechanical tests will be checked (separation, drop and fit check etc.).
- The payload release mechanism will be tested with FSW.
- The CanSat's subsystems durability before and after the test flights will be checked.
- The CanSat will be checked for the given environmental test requirements.
- Thanks to the folding mechanism designers in our team. It fits well into the container.
- The camera stabilization will be achieved by actively controlling payload with rudder and elevator using servo motors

# Decent Control

- The installed electronic circuit will be placed in the payload and it will be tested at 450 meters via the drone.
- The payload’s delta wings will be tested for gliding in a circular pattern with a radius of 250 meters from 450 meters to above 100 meters (actively controlled for one minute). Its aerodynamic suitability will also be checked during the test.
- Active control of the payload will be provided with rudder and elevator using the servo motors. The opening of the payload’s parachute will be tested at an altitude above 100 meters.

# FSW

- The accuracy of the data get from the each sensors were checked (particulate/dust, air speed, GPS location, temperature, pressure, etc.).
- Sub-systems were tested (release mechanisms, parachute opening, communication, etc.).
- Data recovery algorithms were tested in case of microcontroller reset.
- The sequence of the data transmission to the ground station will be checked for consistency in the appropriate order.

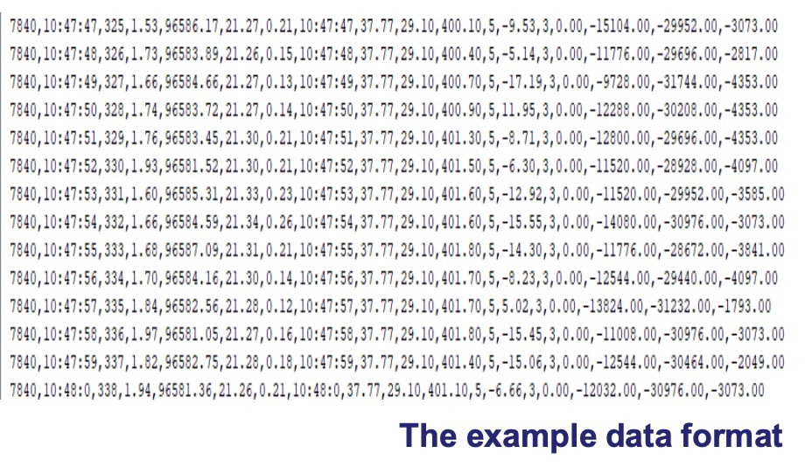
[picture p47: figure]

CANSAT India Students Competition by ASI: Team Id:2022ASI-002 AstroPeep

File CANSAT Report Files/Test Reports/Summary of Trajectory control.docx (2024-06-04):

# Summary of Trajectory control:

1. The average wind speed of DHOLERA is thy month of June is 20km/hr. that’s why we consider the horizontal velocity of our CanSat is to be 20km/hr.
2. In the first line of decent i.e. from 850 m to 500 m the vertical velocity of CanSat is 20km/hr. Thus during this period of time our CanSat travels the horizontal distance of 350 m.
3. In the second line of our decent i.e. from 500m to ground our CanSat travels the speed of 4km/hr. thus the horizontal distance travel by our CanSat is 2500 m
4. Thus when combining the horizontal distance travelled in the first as well as second line of decent is 2500m plus 350m is equal to 2850m i.e. 2.85 km
5. Thus we know how far our CanSat can reach from our ground station, thus we know that we have to design antenna with the range of 3-4 km, so that we can communicate with our CanSat when it reach to ground.

# Design of Parachute:

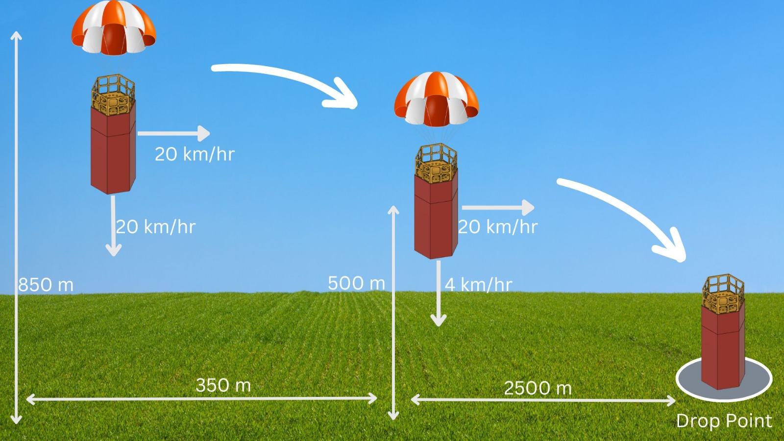
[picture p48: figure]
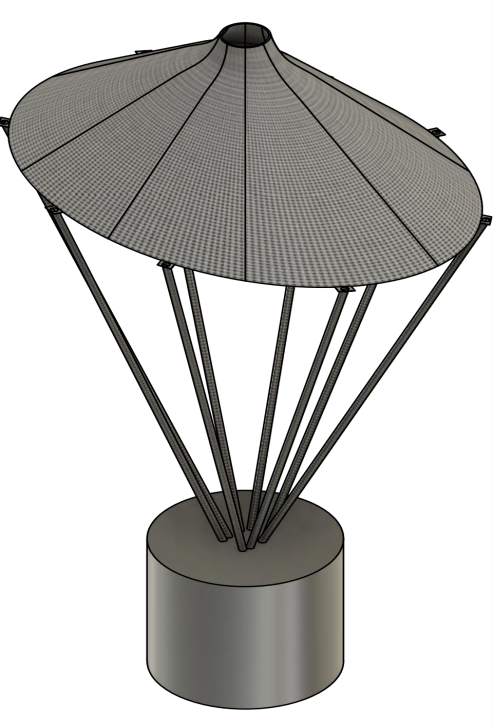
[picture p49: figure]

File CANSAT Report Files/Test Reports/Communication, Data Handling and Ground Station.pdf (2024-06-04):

CANSAT India Students Competition by ASI:

Team Id:2022ASI-002 AstroPeep

# Communication and Data Handling Subsystem Design

## Below is the communication Subsystem overview :

Fig. Communication and Data Handling Overview

Changes made after PDR in communication subsystem and data handling :

PDR | CDR | Rationale

Main processor
was STM32F103

Main processor is changed to ATMega-328.

Due to problems faced in programming STM32F103 and because of previous experience of team in working with ATMega-328 and also meets all the requirements.

# Telemetry

- Upon powering up, the CANSAT collects the required telemetry at a 1 Hz sample rate.
- The telemetry data is being transmitted with ASCII comma separated fields followed by a carriage return in the following format :
- <TEAMID>,<TIMESTAMPING>,<PACKETCOUNT>,<ALTITUDe>,<PRESSURE >,<TEMP>,<VOLTAGE>,<GPSTIME>,<GPS LATITUDE>,<GPS LONGITUDE>, <GPS ALTITUDE>,<GPS SATS>,<ACCELEROMETER DATA>, <GYRO SPIN RATE>, <FLIGHT SOFTWARE STATE>,<ANY OPTIONAL DATA>
- The received telemetry for the entire mission will be saved on the ground station computer as a comma-separated value (.csv) file with name of file as 2022-ASI-002.csv

The NET ID/PAN ID of the Xbee is set to team no. as per the requirements and its setting is shown below :

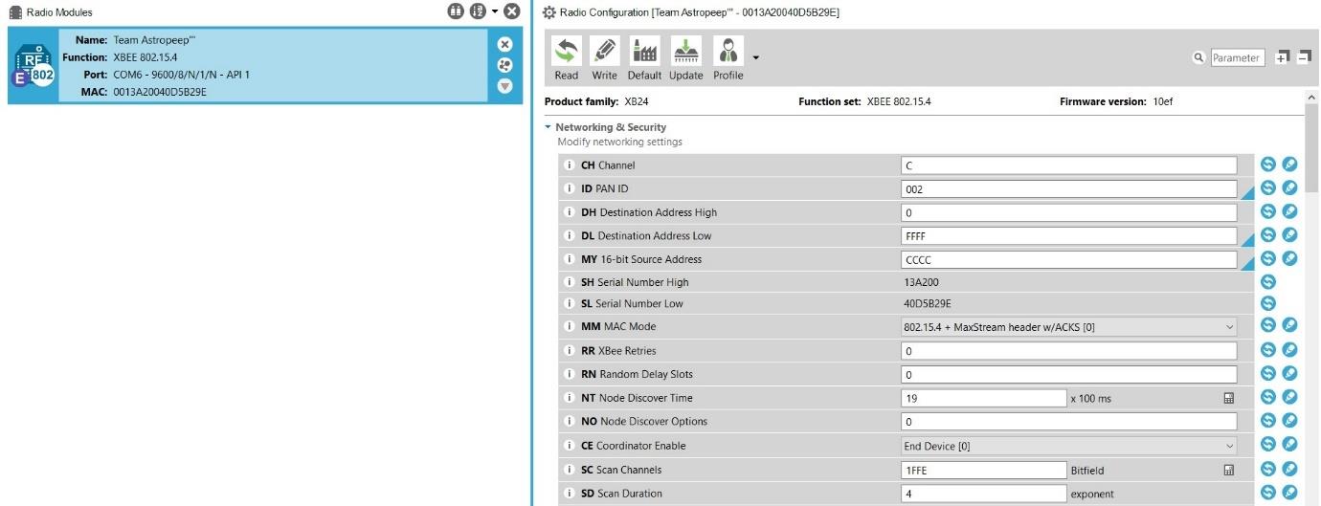
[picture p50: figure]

Fig. . Xbee 1 Setting for NET/PAN ID


Fig. Xbee 2 Setting for NET/PAN ID

# TELEMETRY DATA FORMAT

TM Parameter | Function | Resolution /Format
<TEAM ID> | Team Number | 2022ASI-002
<TIME STAMPING> | Time since the initial power | Seconds
<PACKET COUNT> | Count of transmitted packets | Integer
<ALTITUDE> | Altitude in units of meters and must be relative to ground | 0.1 meters
<PRESSURE> | Measurement of atmospheric pressure | 1 pascal
<TEMP> | Temperature in Celsius | 0.01℃
<VOLTAGE> | Voltage of the CANSAT power bus | 0.01 Volts
<GPS TIME> | Time generated by the GPS receiver | Seconds
<GPS LATITUDE> | Latitude generated by the GPS receiver | 0.0001 degrees
<GPS LONGITUDE> | Longitude generated by the GPS receiver | 0.0001 degrees
<GPS ALTITUDE> | Altitude generated by the GPS receiver | 0.1 meters

# Communication and Link Budget

Some changes are done in which we revisited the Gain calculation of receiving and transmitting antenna and we rectified accordingly as shown below.


Fig. Communication and Link Budget

# Calculation :

- Transmitted Power : 8 dB
- Transmitter Antenna Gain : 5.94 dB
- Transmitter Loss : 1 dB
- Free Space Loss : 110.14 dB
- Miscellaneous Loss : 1 dB
- Receiver Antenna Gain : 11.1 dB
- Receiver Loss : 1 dB
- Received Power : -84.14 dB
- Receiver Sensitivity : -101 dB
- Link Margin : 16.86 dB

# Antenna Selection

There is no changes since PDR just we simulated the radiation pattern of antennas and found the gains accordingly.

## GCS Antenna

Antenna Design :


Antenna Radiation Pattern :

Antenna Design Code :

## CANSAT Antenna


Antenna Design :

Antenna Radiation Pattern :

Antenna Design Code :


The gain obtained after analysis are :

- GCS Antenna – 11.1 db
- Cansat Antenna – 5.94 db

An after calculating we rectified the changes in the Communication and Link Budget.

# Electrical POWER SUBSYSTEM

## There are only some minor changes in Electrical power subsystem as mentioned below :

- The battery configuration is changed from series to parallel which made the step down process more efficient.
- The position of switch is also modified from bottom to panel side of CANSAT.

# Electrical Block Diagram


Fig. Electrical Power Subsystem Block Diagram

# Flight Software design

## Overview of the CanSat FSW Design

- The CanSat will collect sensor data then save to SD card and send to ground station via XBee.
- The CanSat will deploy 2nd Parachute deploy mechanism after reaching 500m altitude.
- The buzzer will keep beeping after landing until turned off with power switch.

## Programming Language

- C/C++ for CanSat container
- Python/C++ for ground station

## Development Environment

- Arduino IDE
- Visual Studio Code
- Spyder


Fig. Flight Software Design Overview

## Momentary Power Cut Precaution Strategy :

As far as power management goes, all devices are ON for all time except two (Servo motor for Deployment of 2nd Parachute and Buzzer for recovery) as Servo motor will deployed only for some time after crossing critical altitude (500m) and Buzzer will be turned ON after landing for location and recovery of CanSat.

After reset of processor in flight mode, previous state of mission together with last packet count can be retrieved from flash.

This information with current GNSS time is sufficient to continue mission.

# GCS Design and Overview

## Overview

- Main Computer is a laptop running GS application. The application is configured in GUI so that an appropriate port and baud rate can be selected.
- QHA antenna receives data from the probe (i.e. CanSat CPU) and transmits commands.
- Xbee PRO S2C module forwards and receive data to form communication link between CanSat and GCS.
- GS application, written in C++/Python, saves and displays data. It also saves received data in a local area network.

There is no changes since PDR.

## Data Flow and Components

- The antenna receives data over radio from the probe.
- Using Xbee explorer cable , forwards data to the Xbee module.
- Xbee PRO S2C module forwards data to GS’s Main Computer using micro USB to USB cable.
- Software developed in C++ parses and then displays data in engineering units and save them into a CSV file.
- Main computer is capable of sending predefined commands to the probe.

## Progress Since PDR :

- The login page of GUI is completed and currently working on dashboard page of GUI and the overall data receiving software is tested for sensors individually.
- The development of helical antenna of GCS is started.

## Ground Control Station GUI :


Fig. GCS GUI login page

The GUI is build using SPYDER IDE using Python language and the work is still in progress the login page is build as shown above and the dashboard work is in progress and for testing we individually tested the sensor by sending data using our microprocessor and plotted graph in the SPYDER IDE using Python function matplotlib.


The screenshots of code written in SPYDER IDE are attached below :



The development of dashboard were all the data will be plotted is in progress and after development the dashboard will be like as shown below :


Fig. GCS GUI Dashboard

# CANSAT algorithm

The CANSAT algorithm is developed in C/C++ language using Visual Studio Code and Arduino IDE and the flow chart of the algorithm is shown below :


Fig. Cansat Algorithm Flow Chart

# Ground Station final test results

The Cansat Ground Station final test results is still in progress as the test of data collection is done individually for all the sensors and in next step we will be combining the overall data into our GUI.

Our GUI work is also still in progress and final glimpse of our GUI is shown below :


The test result plots of the individual sensor data are shown below :

Fig. CANSAT GUI Dashboard

Altitude Test Plot :

Pressure Test Plot :

Temperature Test Plot :


The testing of some of the components are still in progress like GPS , Gyroscope and Accelerometer.We are still working on the testing of the above mentioned components.


# CANSAT Integration and Testing

## Testing before Integration :



The above mentioned steps are for testing the cansat before integration and after this testing we will go ahead for integration.

## Integration of CANSAT :

- As our primary structure fabrication process which will let be a homogenous structure with no mechanical joints.
- Other than this the outer body panels will be connected using the shock absorbing screws.
- Batteries , PCB and Servo motors are connected to the particular damper used which are then connected to the structure of CANSAT using screws and other mechanical joints as shown below.


Fig. CANSAT Integration Stage 1


Fig. CANSAT Integration Stage 2

# Mission Operation and Analysis


# Pre-flight requirement-check-analysis

## Setting up GS

• Computer and Antenna; Communication Test; Pre-Flight check and Tests; • Structure • Electronics • DCS components

## Cansat Integration

- Container assembly

## CanSat recovery

# Logistics and transportation:

For the Logistics and Transportation:

- We will be packing the fragile and non secured elements independently using cartons and bubble wraps.
- Whereas other all the elements will be packed in a wooden sheet box by using Thermocol sheets, Bubble Wraps, Cardboard and Straps as per the requirements of the fabricated model of CANSAT.

# CANSAT ready to launch and final comments

- The testing were made on similar kind of prototypes and we found the rectifications in the model as observed.
- Accordingly we have made changes and as of that our software part is almost done however in Hardware our work is still in progress.
- Due to the delay in the delivery of the materials and the electronic components required for the final fabrication of the CANSAT.
- The work will be completed in accordance to the availability of material however all the analysis , simulations and test results are completed through the alternative scale models of the similar materials.

# Conclusion

## Accomplishments

- Telemetry is tested.
- GCS GUI is developed up to some extent.
- Antenna testing is completed.
- Mechanical analysis (Stress-strain , Vibration and Fit check) is completed.

## Unfinished work

- The fully integrated electronic & mechanical subsystem are not entirely functional yet and needs to be tested.
- Prototypes are being tested and more refinements are required.
- Flight software is in progress.

## Next stage of development

- Final Fabrication work completion
- Code Review
- Testing of integrated system
- Assembly of complete CANSAT
- Integrated testing of CANSAT.

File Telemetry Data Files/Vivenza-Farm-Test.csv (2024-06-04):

"""2022ASI-002"",""0:0:0"",108,73.86282349,99623.17188,40.64706039,0.200000003,""0:0:0"",0,0,0,0,0.319054663,0.34318164,1.463775873,58.0134964,9.42641449,-24.75930023,""Ascent"",-174.9364319,-80.76583862,-2248.688477"
"""2022ASI-002"",""0:0:0"",109,73.46074677,99627.92188,40.78823471,0.200000003,""0:0:0"",0,0,0,0,0.273400366,0.242351562,1.428863764,46.96006012,-0.054501534,-28.01120949,""Ascent"",-131.9927521,-79.40975189,-2272.582031"
"""2022ASI-002"",""0:0:0"",110,73.56455231,99626.69531,40.78823471,0.200000003,""0:0:0"",0,0,0,0,0.020714819,-0.41853711,1.331207514,74.12036133,9.518017769,-7.400522232,""Ascent"",-67.74175262,-69.88207245,-2278.894775"
"""2022ASI-002"",""0:0:0"",111,73.41213226,99628.5,40.74117661,0.200000003,""0:0:0"",0,0,0,0,0.103966773,-0.274494141,1.573639154,45.02112961,26.03710175,-38.48449326,""Ascent"",-28.94942665,-46.79345322,-2311.722168"
"""2022ASI-002"",""0:0:0"",112,73.27338409,99630.14063,40.83529282,0.200000003,""0:0:0"",0,0,0,0,0.144738257,-0.248126954,1.505035639,30.79211998,-3.398013115,-29.59899521,""Ascent"",-2.846641302,-48.80319977,-2336.94043"
"""2022ASI-002"",""0:0:0"",113,73.3549118,99629.17188,40.78823471,0.200000003,""0:0:0"",0,0,0,0,0.190880835,-0.118976563,1.487701654,49.43334198,10.44931507,-14.19441509,""Ascent"",38.24911499,-39.27886581,-2348.991455"
"""2022ASI-002"",""0:0:0"",114,73.72153473,99624.84375,40.78823471,0.200000003,""0:0:0"",0,0,0,0,0.085167944,-0.298908204,1.488434076,31.25013542,22.51038361,-23.61426353,""Ascent"",63.3500061,-19.76223564,-2369.11084"
"""2022ASI-002"",""0:0:0"",115,73.67798615,99625.35156,40.74117661,0.200000003,""0:0:0"",0,0,0,0,0.140587866,-0.25056836,1.568756342,44.86845779,11.27374268,-28.8051033,""Ascent"",99.40956116,-10.04396343,-2393.681641"
"""2022ASI-002"",""0:0:0"",116,73.61823273,99626.0625,40.74117661,0.200000003,""0:0:0"",0,0,0,0,0.078576148,-0.309650391,1.570221186,41.21960068,16.96839905,-25.17151451,""Ascent"",131.6152496,4.26863575,-2415.127686"
"""2022ASI-002"",""0:0:0"",117,73.77571869,99624.20313,40.88235474,0.200000003,""0:0:0"",0,0,0,0,0.141076148,-0.288898438,1.487945795,39.11273193,11.56381893,-27.72113228,""Ascent"",161.4217224,13.73223972,-2438.746094"
"""2022ASI-002"",""0:0:0"",118,73.64051056,99625.79688,40.74117661,0.200000003,""0:0:0"",0,0,0,0,0.197960913,-0.045490235,1.64614892,42.19670105,27.91496277,-11.36998844,""Ascent"",-159.3228912,36.68309402,-2448.456055"
"""2022ASI-002"",""0:0:0"",119,73.32756805,99629.5,40.74117661,0.200000003,""0:0:0"",0,0,0,0,0.062951148,-0.085041016,1.41958642,7.051662445,40.38824844,-28.02647591,""Ascent"",-150.3239899,69.58174133,-2472.306641"
"""2022ASI-002"",""0:0:0"",120,73.13159943,99631.82031,40.78823471,0.200000003,""0:0:0"",0,0,0,0,-0.05716604,-0.169513673,1.413971186,75.58601379,-13.36747837,-25.41579056,""Ascent"",-84.41690063,57.08787155,-2493.935547"
"""2022ASI-002"",""0:0:0"",121,73.11792755,99631.98438,40.78823471,0.200000003,""0:0:0"",0,0,0,0,0.376671851,0.017742187,1.288971186,32.41044235,2.159238815,-18.3776207,""Ascent"",-55.65200043,57.4232254,-2509.593262"
"""2022ASI-002"",""0:0:0"",122,72.59283447,99638.1875,40.74117661,0.200000003,""0:0:0"",0,0,0,0,0.290978491,0.163738281,1.230621576,232.7615814,-17.90182877,-42.40815735,""Ascent"",140.4114227,41.02854156,-2545.809814"
"""2022ASI-002"",""0:0:0"",123,72.07030487,99644.375,40.83529282,0.200000003,""0:0:0"",0,0,0,0,0.141564429,0.153728515,1.373687983,51.57074738,34.35771179,-46.65243149,""Ascent"",-179.1596985,68.81200409,-2585.604248"
"""2022ASI-002"",""0:0:0"",124,72.7244873,99636.63281,40.88235474,0.200000003,""0:0:0"",0,0,0,0,0.311242163,0.057781249,1.54458642,-51.17734528,52.96839905,-19.06464386,""Ascent"",134.4842987,-64.91353607,-2601.866455"
"""2022ASI-002"",""0:0:0"",125,72.27232361,99641.98438,40.92941284,0.200000003,""0:0:0"",0,0,0,0,0.374962866,0.126873046,1.677643061,59.58601379,0.327177525,-21.33945465,""Ascent"",-171.0522308,-63.59272385,-2620.090332"
"""2022ASI-002"",""0:0:0"",126,72.90221405,99634.53125,40.92941284,0.200000003,""10:50:57"",0,0,0,0,0.289757788,0.192546874,1.608062983,73.55548096,-5.214806557,-37.72113419,""Ascent"",-106.0808868,-66.87789917,-2652.22876"
"""2022ASI-002"",""10:50:57"",127,72.81360626,99635.58594,40.97647095,0.200000003,""10:50:58"",0,0,0,0,0.221886694,-0.085773438,1.647857904,14.7310524,26.00656891,-31.24785042,""Ascent"",-91.73292542,-44.00455475,-2678.820801"
"""2022ASI-002"",""10:50:58"",128,72.26473236,99642.07031,40.97647095,0.200000003,""10:50:59"",0,0,0,0,0.159386694,0.027751952,1.547516108,82.3799057,-2.772058487,-9.003576279,""Ascent"",-21.01317215,-45.55932999,-2686.500732"
"""2022ASI-002"",""10:50:59"",129,72.0824585,99644.23438,41.07058716,0.200000003,""10:51:0"",0,0,0,0,0.223595679,-0.088703126,1.606842279,37.06692886,4.174506187,-32.77456665,""Ascent"",10.29390144,-41.32080078,-2714.424561"
"""2022ASI-002"",""10:51:0"",130,72.15081024,99643.42188,41.02352905,0.200000003,""10:51:1"",0,0,0,0,0.198937476,-0.060626954,1.61489892,58.5173111,13.59435272,-25.29365158,""Ascent"",58.96230698,-29.27067947,-2736"
"""2022ASI-002"",""10:51:1"",131,72.54979706,99638.28906,41.07058716,0.200000003,""10:51:1"",0,0,0,0,0.296105444,0.001140624,1.691803217,41.37227249,2.815727472,-35.58372879,""Ascent"",92.40911102,-26.52728081,-2766.388428"
"""2022ASI-002"",""10:51:1"",132,72.33966827,99641.1875,41.07058716,0.200000003,""10:51:2"",0,0,0,0,0.317101538,0.063640624,1.626129389,46.66998291,25.5027504,-29.21731567,""Ascent"",129.4810181,-4.973466873,-2791.223145"
"""2022ASI-002"",""10:51:2"",133,72.13764191,99643.57813,41.21176529,0.200000003,""10:51:3"",0,0,0,0,0.226281226,-0.016681641,1.626373529,45.86082077,10.99893379,-22.97304153,""Ascent"",165.0818329,4.129706383,-2810.750244"
"""2022ASI-002"",""10:51:3"",134,72.37358856,99640.78125,41.11764526,0.200000003,""10:51:2"",0,0,0,0,0.209923804,-0.097248048,1.635650873,50.07456207,12.57145309,-22.19441605,""Ascent"",-149.2279816,14.4100771,-2829.682129"
"""2022ASI-002"",""10:51:2"",135,72.4546051,99639.82813,41.16470718,0.200000003,""10:51:4"",0,0,0,0,0.203332007,-0.147785157,1.619049311,46.05929565,7.212674141,-16.71349907,""Ascent"",-107.8441162,20.00866318,-2843.938721"
"""2022ASI-002"",""10:51:4"",136,72.14827728,99643.45313,41.25882339,0.200000003,""10:51:5"",0,0,0,0,0.191613257,-0.159503907,1.614410639,45.64708328,6.800460339,-25.56846046,""Ascent"",-67.55161285,25.17187309,-2865.799805"
"""2022ASI-002"",""10:51:5"",137,72.49612427,99639.33594,41.21176529,0.200000003,""10:51:6"",0,0,0,0,0.200890601,-0.152423829,1.610016108,48.39517212,8.800459862,-26.74403381,""Ascent"",-25.80503082,31.89209747,-2888.63916"
"""2022ASI-002"",""10:51:6"",138,71.5483017,99650.54688,41.40000153,0.200000003,""10:51:6"",0,0,0,0,0.198205054,-0.158771485,1.610748529,51.57074738,9.976032257,-21.82800293,""Ascent"",17.65882874,39.44421387,-2907.236572"
"""2022ASI-002"",""10:51:6"",139,72.9234848,99634.28125,41.35293961,0.200000003,""10:51:7"",0,0,0,0,0.274621069,0.216716796,1.36880517,-80.56665802,74.93785858,-81.50739288,""Ascent"",-49.62990189,-75.54559326,-2976.517822"
"""2022ASI-002"",""10:51:7"",140,73.33567047,99629.40625,41.35293961,0.200000003,""10:51:8"",0,0,0,0,0.339806616,0.592693329,1.754791498,83.78448486,8.479849815,-20.24021721,""Ascent"",21.60418892,-67.170578,-2993.742188"
"""2022ASI-002"",""10:51:8"",141,73.88510132,99622.90625,41.35293961,0.200000003,""10:51:9"",0,0,0,0,0.258996069,0.569011688,1.628082514,57.70815277,11.19740677,-34.69823074,""Ascent"",69.79351044,-56.63761902,-3023.339844"
"""2022ASI-002"",""10:51:9"",142,73.52455139,99627.17188,41.3058815,0.200000003,""10:51:10"",0,0,0,0,0.279503882,0.348064452,1.371978998,83.06692505,-8.375112534,-7.095178604,""Ascent"",138.1972198,-62.73757553,-3029.39917"
"""2022ASI-002"",""10:51:10"",143,73.94688416,99622.17188,41.3058815,0.200000003,""10:51:11"",0,0,0,0,0.262414038,0.476238281,1.393951654,29.05166245,-8.375112534,-39.79747009,""Ascent"",160.08992,-68.68593597,-3063.346436"
"""2022ASI-002"",""10:51:11"",144,73.41213226,99628.5,41.44705963,0.200000003,""10:51:12"",0,0,0,0,0.203576148,0.323894531,1.308258295,74.80738831,-16.52778244,-19.7364006,""Ascent"",-133.1024628,-81.30024719,-3080.181641"
"""2022ASI-002"",""10:51:12"",145,73.44150543,99628.15625,41.35293961,0.200000003,""10:51:12"",0,0,0,0,0.207238257,0.353191406,1.226715326,55.67761612,0.159238815,-12.49975872,""Ascent"",-83.52573395,-79.72540283,-3090.856445"
"""2022ASI-002"",""10:51:12"",146,73.48200989,99627.67188,41.40000153,0.200000003,""10:51:13"",0,0,0,0,0.201378882,0.392498046,1.128082514,50.60891342,11.15160561,-44.10281372,""Ascent"",-39.22065353,-69.01115417,-3128.432129"
"""2022ASI-002"",""10:51:13"",147,73.66988373,99624.5625,41.40000153,0.200000003,""10:51:14"",0,0,0,0,0.205285132,0.446941406,1.195465326,67.05166626,26.98366547,-55.67533112,""Ascent"",18.01947594,-45.25695801,-3175.923096"
"""2022ASI-002"",""10:51:14"",148,73.8025589,99623.88281,41.44705963,0.200000003,""10:51:15"",0,0,0,0,0.175988257,0.640789032,1.155670404,57.05166245,23.12107086,-37.21731567,""Ascent"",65.92544556,-25.17571259,-3207.669434"
"""2022ASI-002"",""10:51:15"",149,73.46074677,99627.92188,41.44705963,0.200000003,""10:51:16"",0,0,0,0,0.200890601,0.603679657,1.387115717,62.80738831,21.83862686,-22.04174423,""Ascent"",117.699295,-6.524899483,-3226.515137"
"""2022ASI-002"",""10:51:16"",150,73.51441956,99627.28906,41.40000153,0.200000003,""10:51:17"",0,0,0,0,0.222130835,0.54630661,1.469391108,42.5173111,13.88442993,-21.81273651,""Ascent"",151.3325806,5.064457893,-3245.143311"
"""2022ASI-002"",""10:51:17"",151,73.43694305,99628.20313,41.3058815,0.200000003,""10:51:18"",0,0,0,0,0.271691382,0.567790985,1.440338373,26.48677635,5.86916256,1.225431442,""Ascent"",170.8708038,9.670370102,-3244.0979"
"""2022ASI-002"",""10:51:18"",152,73.36301422,99629.08594,41.54117584,0.200000003,""10:51:18"",0,0,0,0,0.230187476,0.382976562,1.363434076,2.288303375,33.67068863,-9.079912186,""Ascent"",169.6714172,37.37300491,-3251.824951"
"""2022ASI-002"",""10:51:18"",153,73.26274872,99630.26563,41.35293961,0.200000003,""10:51:19"",0,0,0,0,0.283410132,0.27286914,1.366119623,31.98295975,8.815727234,-19.29365158,""Ascent"",-159.6588898,43.73906326,-3268.224609"
"""2022ASI-002"",""10:51:19"",154,73.39896393,99628.65625,41.35293961,0.200000003,""10:51:20"",0,0,0,0,0.256554663,0.270183593,1.386383295,51.00585938,7.762291908,-23.85853767,""Ascent"",-113.6109161,49.14719772,-3288.575928"
"""2022ASI-002"",""10:51:20"",155,73.3579483,99629.14063,41.44705963,0.200000003,""10:51:21"",0,0,0,0,0.273644507,0.263347656,1.400299311,43.81502151,13.15160561,-27.90433884,""Ascent"",-74.45987701,58.95366669,-3312.40625"
"""2022ASI-002"",""10:51:21"",156,73.34022522,99629.35156,41.40000153,0.200000003,""10:51:22"",0,0,0,0,0.275353491,0.234539062,1.415436029,45.28067017,18.08290291,-24.48449135,""Ascent"",-34.88961792,72.69126129,-3333.315918"
"""2022ASI-002"",""10:51:22"",157,73.56201935,99626.72656,41.54117584,0.200000003,""10:51:23"",0,0,0,0,0.289269507,0.282878906,1.418609858,50.85318756,15.24320793,-22.14861298,""Ascent"",8.539497375,87.35368347,-3352.20874"
"""2022ASI-002"",""10:51:23"",158,73.31946564,99629.59375,41.35293961,0.200000003,""10:51:23"",0,0,0,0,0.234337866,0.213542968,1.385162592,45.18906784,0.067635536,-27.00357628,""Ascent"",46.36119843,89.07337189,-3375.269775"
"""2022ASI-002"",""10:51:23"",159,73.71292877,99624.9375,41.40000153,0.200000003,""10:51:24"",0,0,0,0,0.299523413,0.217449218,1.473541498,52.15089798,11.09053612,-23.90433884,""Ascent"",89.14246368,-80.0753479,-3395.63623"
"""2022ASI-002"",""10:51:24"",160,73.47543335,99627.75,41.49411774,0.200000003,""10:51:25"",0,0,0,0,0.281457007,0.209636718,1.417389154,48.50204468,4.632521152,-23.232584,""Ascent"",127.9744415,-74.83267975,-3415.407227"
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

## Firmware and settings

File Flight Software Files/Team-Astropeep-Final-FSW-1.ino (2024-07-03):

#include <Wire.h>
#include <SoftwareSerial.h>
#include <Adafruit_BMP280.h>
#include <MPU6050_light.h>
#include <TinyGPS++.h>
#include <ArduinoJson.h>

Adafruit_BMP280 bmp;
MPU6050 mpu(Wire);
TinyGPSPlus gps;

#define MPU_ADDR 0x68
#define BMP_SCK 13
#define BMP_MISO 12
#define BMP_MOSI 11
#define BMP_CS 10
#define GPS_RX_PIN 2
#define GPS_TX_PIN 3

char tmp_str[7];
char* convert_int16_to_str(int16_t i){
return tmp_str;
}

SoftwareSerial gpsSerial(GPS_RX_PIN, GPS_TX_PIN);
SoftwareSerial xbeeSerial(4, 5);

DynamicJsonDocument jsonDoc(512);

String TelemetryPackage;
int PacketCount;
int Count;
const String Team_Id = "2022ASI-002";
String FSW_State = "";
String TimeStamp;
String GpsTime;
float Pressure, Temperature, Altitude, Voltage, GpsLatitude, GpsLongitude, GpsAltitude, GpsSats;
float a_x, a_y, a_z, gyro_x, gyro_y, gyro_z;

void setup() {
  Serial.begin(9600);
  gpsSerial.begin(9600);
  Wire.begin();
  mpu.begin();
  mpu.calcOffsets(true, true);
  Wire.write(0);
  Wire.endTransmission(true);
  if (!bmp.begin(0x76)) {
    Serial.println(F("Could not find a valid BMP280 sensor, check wiring!"));
  }
}

void loop() {
  mpu.update();

  while (gpsSerial.available() > 0) {
    gps.encode(gpsSerial.read());
  }
  
  if (gps.date.isValid() && gps.time.isValid()) {
    GpsTime = String(gps.time.hour()) + ":" + String(gps.time.minute()) + ":" + String(gps.time.second());
  }

  Pressure = getPressure();
  Temperature = getTemperature();
  Altitude = getAltitude();
  Temperature = mpu.getTemp();
  gyro_x = mpu.getGyroX();
  gyro_y = mpu.getGyroY();
  gyro_z = mpu.getGyroZ();
  a_x = mpu.getAccX();
  a_y = mpu.getAccY();
  a_z = mpu.getAccZ();
  Voltage = getVolt();
  GpsLatitude = getGPSlat();
  GpsLongitude = getGPSlon();
  GpsAltitude = getGPSalti();
  GpsSats = getGPSsats();
  Voltage = getVolt();
  TimeStamp = GpsTime;

  float ref_height = 213.46;
  float ref_alt = GpsAltitude - ref_height;

  if (Altitude == ref_alt && Count == 0){
    FSW_State = "Ground";
  }

  else if (Altitude > 100 && Count == 0){
    Count++;
  }

  else if (Altitude < 500 && Altitude > 100 && Count == 1){
    FSW_State = "Descent";
  }

  else if (Altitude < 100 && Count == 1){
    FSW_State = "Landing";
  }

  else {
    FSW_State = "Ascent";
  }


  jsonDoc["Team_Id"] = Team_Id;
  jsonDoc["TimeStamp"] = TimeStamp;
  jsonDoc["PacketCount"] = PacketCount;
  jsonDoc["Altitude"] = Altitude;
  jsonDoc["Pressure"] = Pressure;
  jsonDoc["Temperature"] = Temperature;
  jsonDoc["Voltage"] = Voltage;
  jsonDoc["GpsTime"] = GpsTime;
  jsonDoc["GpsLatitude"] = GpsLatitude;
  jsonDoc["GpsLongitude"] = GpsLongitude;
  jsonDoc["GpsAltitude"] = GpsAltitude;
  jsonDoc["GpsSats"] = GpsSats;
  jsonDoc["a_x"] = a_x;
  jsonDoc["a_y"] = a_y;
  jsonDoc["a_z"] = a_z;
  jsonDoc["gyro_x"] = gyro_x;
  jsonDoc["gyro_y"] = gyro_y;
  jsonDoc["gyro_z"] = gyro_z;
  jsonDoc["FSW_State"] = FSW_State;
  jsonDoc["mpu.getAngleX()"] = mpu.getAngleX();
  jsonDoc["mpu.getAngleY()"] = mpu.getAngleY();
  jsonDoc["mpu.getAngleZ()"] = mpu.getAngleZ();




  TelemetryPackage =  Team_Id + "," + TimeStamp + "," + String(PacketCount) + "," + String(Altitude) + "," + String(Pressure) + "," + String(Temperature) + "," + String(Voltage)
                      + "," + GpsTime + "," + String(GpsLatitude) + "," + String(GpsLongitude) + "," + String(GpsAltitude) + "," + String(GpsSats) + "," + String(a_x)
                      + "," + String(a_y) + "," + String(a_z)+ "," + String(gyro_x) + "," + String(gyro_y) + "," + String(gyro_z) + "," + String(FSW_State) + "," + String(mpu.getAngleX()) + "," + String(mpu.getAngleY()) + "," + String(mpu.getAngleZ());


  // Serial.println(String(GpsSats) + "," + String(GpsAltitude) + "," + String(GpsLongitude) + "," + String(GpsLatitude) + "," + GpsTime);
  // Serial.println(String(Temperature) + "," + String(a_x) + "," + String(a_y) + "," + String(a_z) + "," + String(gyro_x) + "," + String(gyro_y) + "," + String(gyro_z));

  String jsonData;
  serializeJson(jsonDoc, jsonData);
  const char* dataPacket = jsonData.c_str();
  sendPacket(dataPacket);

  Serial.println(dataPacket);

  delay(1);

  PacketCount++;

}

// Defining Functions

float getPressure() {
  float pressure = bmp.readPressure();
  return pressure;
}

float getTemperature() {
  float temp = bmp.readTemperature();
  return temp;
}

float getAltitude() {
  float alti = bmp.readAltitude(1005);
  return alti;
}

float getVolt() {
  int offset = 20;
  int volt = analogRead(A1);
  double voltage = map(volt, 0, 1023, 0, 2500) + offset;
  voltage /= 100;
  return voltage;
}

float getGPSlat() {
  float lat = 0;
  if (gps.location.isValid()) {
    lat = gps.location.lat();
  }
  return lat;
}

float getGPSlon() {
  float lon = 0;
  if (gps.location.isValid()) {
    lon = gps.location.lng();
  }
  return lon;
}

float getGPSalti() {
  float alti = 0;
  if (gps.location.isValid()) {
    alti = gps.altitude.meters();
  }
  return alti;
}

int getGPSsats() {
  int sats = 0;
  if (gps.satellites.isValid()) {
    sats = gps.satellites.value();
  }
  return sats;
}

void sendPacket(const char* data) {

  byte startDelimiter = 0x7E;

  byte frameType = 0x10;
  byte frameID = 0x01;

  byte destAddr[] = {0x00, 0x00, 0x00, 0x00, 0x00, 0x00, 0xFF, 0xFF};
  byte destAddr16[] = {0xFF, 0xFE};

  byte options = 0x00;

  byte radius = 0x00;

  char dataCopy[strlen(data) + 1];
  strcpy(dataCopy, data);

  char* token = strtok(dataCopy, ",");
  while (token != NULL) {
    byte* dataBytes = (byte*)token;
    size_t dataLength = strlen(token);

    uint16_t packetLength = 14 + dataLength;

    uint8_t checksum = 0xFF - ((frameType + frameID + destAddr[0] + destAddr[1] + destAddr[2] +
                               destAddr[3] + destAddr[4] + destAddr[5] + destAddr[6] + destAddr[7] +
                               destAddr16[0] + destAddr16[1] + options + radius +
                               sum(dataBytes, dataLength)) & 0xFF);


    xbeeSerial.write(startDelimiter);
    xbeeSerial.write(packetLength >> 8);
    xbeeSerial.write(packetLength & 0xFF);
    xbeeSerial.write(frameType);
    xbeeSerial.write(frameID);
    xbeeSerial.write(destAddr, sizeof(destAddr));
    xbeeSerial.write(destAddr16, sizeof(destAddr16));
    xbeeSerial.write(options);
    xbeeSerial.write(radius);
    xbeeSerial.write(dataBytes, dataLength);
    xbeeSerial.write(checksum);

    delay(10);

    token = strtok(NULL, ",");
  }
}


uint8_t sum(const byte* data, size_t length) {
  uint8_t sum = 0;
  for (size_t i = 0; i < length; i++) {
    sum += data[i];
  }
  return sum;
}

void printPacket(byte value) {
  if (value < 0x10) {
    Serial.print('0');
  }
  Serial.print(value, HEX);
  Serial.print(' ');
}

void printPacket(const byte* data, size_t length) {
  for(size_t i = 0; i < length; i++) {
    printPacket(data[i]);
  }
}

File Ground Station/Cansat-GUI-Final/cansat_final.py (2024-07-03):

import os
import time
import math
import logo_rc
import sys
import requests
import serial
import csv
import folium
from PyQt5 import QtWidgets, QtCore
from PyQt5 import QtWebEngineWidgets
from PyQt5.QtCore import QUrl
from PyQt5.QtWebEngineWidgets import QWebEngineView
from PyQt5.QtWidgets import *
from PyQt5.QtCore import *
from PyQt5.uic import loadUi
from PyQt5.QtGui import *
from PyQt5.QtCore import QTimer
from PyQt5 import QtWidgets
from matplotlib.backends.backend_qt5agg import FigureCanvasQTAgg as FigureCanvas
import matplotlib.pyplot as plt
from matplotlib.figure import Figure
from matplotlib.animation import FuncAnimation
import numpy as np
from pyqtgraph import PlotWidget, plot
import pyqtgraph as pg
import vtk
from vtkmodules.qt.QVTKRenderWindowInteractor import QVTKRenderWindowInteractor
from vtkmodules.util.vtkImageImportFromArray import vtkImageImportFromArray
from vtkmodules.util.colors import tomato
from vtk import vtkOBJReader, vtkPolyDataMapper, vtkActor, vtkRenderer, vtkTransform, vtkCamera

class OpenCameraWindow(QMainWindow):
    def __init__(self, url):
        super().__init__()
        self.setWindowTitle("Astropeep CANSAT Live View")
        self.setGeometry(100, 100, 800, 600)

        self.browser = QWebEngineView()
        self.browser.setUrl(QUrl(url))

        self.setCentralWidget(self.browser)


class MainWindow(QMainWindow):
    def __init__(self):
        super(MainWindow, self).__init__()
        self.setWindowTitle("Astropeep Ground Station")
        self.setupUi()

    def setupUi(self):
        loadUi("cansat_gui_final1_ui.ui", self)
        
        self.start_tele_button = self.findChild(QPushButton, "start_tele_button")
        self.stop_tele_button_2 = self.findChild(QPushButton, "stop_tele_button_2")
        self.save_csv_button = self.findChild(QPushButton, "save_csv_button")
        self.camera_button = self.findChild(QPushButton, "camera_button")
        self.battery_value = self.findChild(QLabel, "battery_value")
        self.fsw_state = self.findChild(QLabel, "fsw_state")
        self.tele_value = self.findChild(QListView, "tele_value")
        self.frame_cansat_view = self.findChild(QFrame, "frame_cansat_view")
        self.mission_time = self.findChild(QLabel, "mission_time")
        self.model = QStandardItemModel()
        self.tele_value.setModel(self.model)
        
        self.frame_alti = QtWidgets.QFrame(self)
        self.frame_pres = QtWidgets.QFrame(self)
        self.frame_temp = QtWidgets.QFrame(self)
        self.frame_accelo = QtWidgets.QFrame(self)
        self.frame_gyro = QtWidgets.QFrame(self)
        self.frame_map = QtWidgets.QFrame(self)
        
        
        self.frame_alti.setGeometry(QtCore.QRect(61, 193, 461, 251))
        self.frame_pres.setGeometry(QtCore.QRect(529, 193, 461, 251))
        self.frame_temp.setGeometry(QtCore.QRect(997, 193, 461, 251))
        self.frame_accelo.setGeometry(QtCore.QRect(61, 503, 461, 251))
        self.frame_gyro.setGeometry(QtCore.QRect(529, 503, 461, 251))
        self.frame_map.setGeometry(QtCore.QRect(997, 503, 461, 251))
    
        
        
        self.frame_alti.setLayout(QtWidgets.QVBoxLayout())
        self.frame_pres.setLayout(QtWidgets.QVBoxLayout())
        self.frame_temp.setLayout(QtWidgets.QVBoxLayout())
        self.frame_accelo.setLayout(QtWidgets.QVBoxLayout())
        self.frame_gyro.setLayout(QtWidgets.QVBoxLayout())
        self.frame_map.setLayout(QtWidgets.QVBoxLayout())
        
        self.vtk_cansat_view = QVTKRenderWindowInteractor(self.frame_cansat_view)
        self.renderer = vtkRenderer()
        self.renderer.SetBackground(0, 181, 226)
        self.vtk_cansat_view.GetRenderWindow().AddRenderer(self.renderer)
        self.load_obj_file("CANSAT@2 v7 v16.obj")
        
        
        
        self.graphWidget_alti = pg.PlotWidget()
        self.graphWidget_pres = pg.PlotWidget()
        self.graphWidget_temp = pg.PlotWidget()
        self.graphWidget_accelo = pg.PlotWidget()
        self.graphWidget_gyro = pg.PlotWidget()
        self.map = QtWebEngineWidgets.QWebEngineView()
        
        self.graphWidget_alti.setBackground('w')
        self.graphWidget_pres.setBackground('w')
        self.graphWidget_temp.setBackground('w')
        self.graphWidget_accelo.setBackground('w')
        self.graphWidget_gyro.setBackground('w')
        
        

        self.frame_alti.layout().addWidget(self.graphWidget_alti)
        self.frame_pres.layout().addWidget(self.graphWidget_pres)
        self.frame_temp.layout().addWidget(self.graphWidget_temp)
        self.frame_accelo.layout().addWidget(self.graphWidget_accelo)
        self.frame_gyro.layout().addWidget(self.graphWidget_gyro)
        self.frame_map.layout().addWidget(self.map)
        
        
        
        self.pc = []
        self.alti = []
        self.pres = []
        self.temp = []
        self.accelo_x = []
        self.accelo_y = []
        self.accelo_z = []
        self.gyro_x = []
        self.gyro_y = []
        self.gyro_z = []
        
        
        
        pen_alti = pg.mkPen(color=(70, 59, 237), width = 1.3)
        pen_pres = pg.mkPen(color=(236, 74, 237), width = 1.3)
        pen_temp = pg.mkPen(color=(237, 74, 78), width = 1.3)
        pen_accelo_x = pg.mkPen(color=(255, 0, 0), width = 1.3)
        pen_accelo_y = pg.mkPen(color=(0, 255, 0), width = 1.3)
        pen_accelo_z = pg.mkPen(color=(0, 0, 255), width = 1.3)
        pen_gyro_x = pg.mkPen(color=(255, 0, 0), width = 1.3)
        pen_gyro_y = pg.mkPen(color=(0, 255, 0), width = 1.3)
        pen_gyro_z = pg.mkPen(color=(0, 0, 255), width = 1.3)
        
        
        self.label_font = QFont("Times", 10, QFont.Bold)
        
        self.graphWidget_alti.setLabel('bottom', "Packet Count")
        self.graphWidget_alti.setLabel('left', "Altitude (m)")
        
        self.graphWidget_pres.setLabel('bottom', "Packet Count")
        self.graphWidget_pres.setLabel('left', "Pressure (Pascal)")
        
        self.graphWidget_temp.setLabel('bottom', "Packet Count")
        self.graphWidget_temp.setLabel('left', "Temperature (\N{SUPERSCRIPT ZERO}C)")
        
        self.graphWidget_accelo.setLabel('bottom', "Packet Count")
        self.graphWidget_accelo.setLabel('left', "Acceleration (m/s\N{SUPERSCRIPT TWO})")
        
        self.graphWidget_gyro.setLabel('bottom', "Packet Count")
        self.graphWidget_gyro.setLabel('left', "Gyro Spin (\N{SUPERSCRIPT ZERO}/s)")
        
        self.graphWidget_accelo.addLegend((330, 0.05))
        self.graphWidget_gyro.addLegend((330, 0.05))
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
